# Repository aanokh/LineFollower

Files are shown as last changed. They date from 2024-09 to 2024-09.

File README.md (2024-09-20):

# __Line Follower Robot__

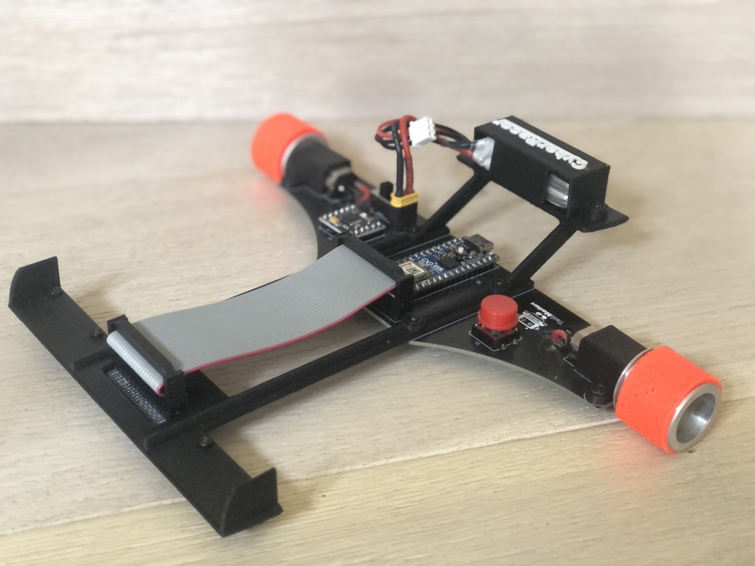
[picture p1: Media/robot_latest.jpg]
An image of the robot


This autonomous line follower robot was created for the RoboGames Olympics 2024 by me and my younger brother. It has been designed, modeled, constructed and programmed from scratch. The robot can autonomously follow a black or white line on a contrasting background at high speeds by implementing a PID controller.

### 3D Design

The bracket and other components of the robot body were designed in Autodesk Fusion 360. They were then sliced in Ultimaker Cuda and 3d printed, first out of plastic and finally from carbon fiber. The main frame was designed to be easily replaceable to test varying robot lengths and multiple prototypes were tried before arriving at the final design.

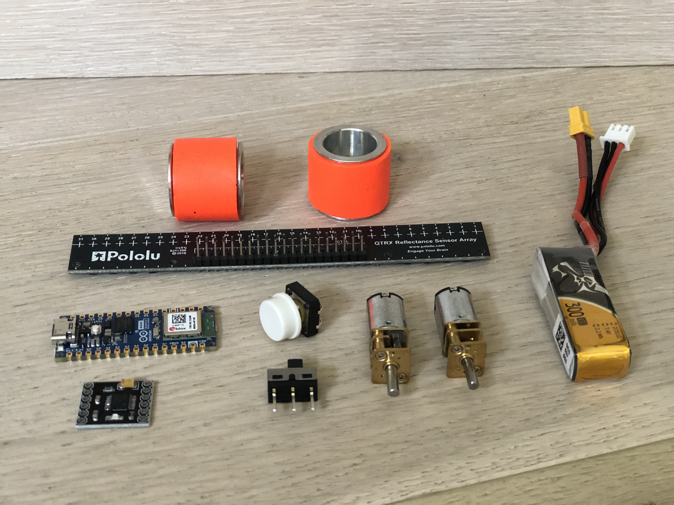
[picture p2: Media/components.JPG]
An image of some of the robot's components


After early testing, it was evident that standard rubber wheels were too slippery and hindered the robot's accuracy especially on sharp turns. To solve this issue, the wheels were upgraded to special JSumo non-slip aluminum silicone wheels that greatly increase the robot's friction with the track.

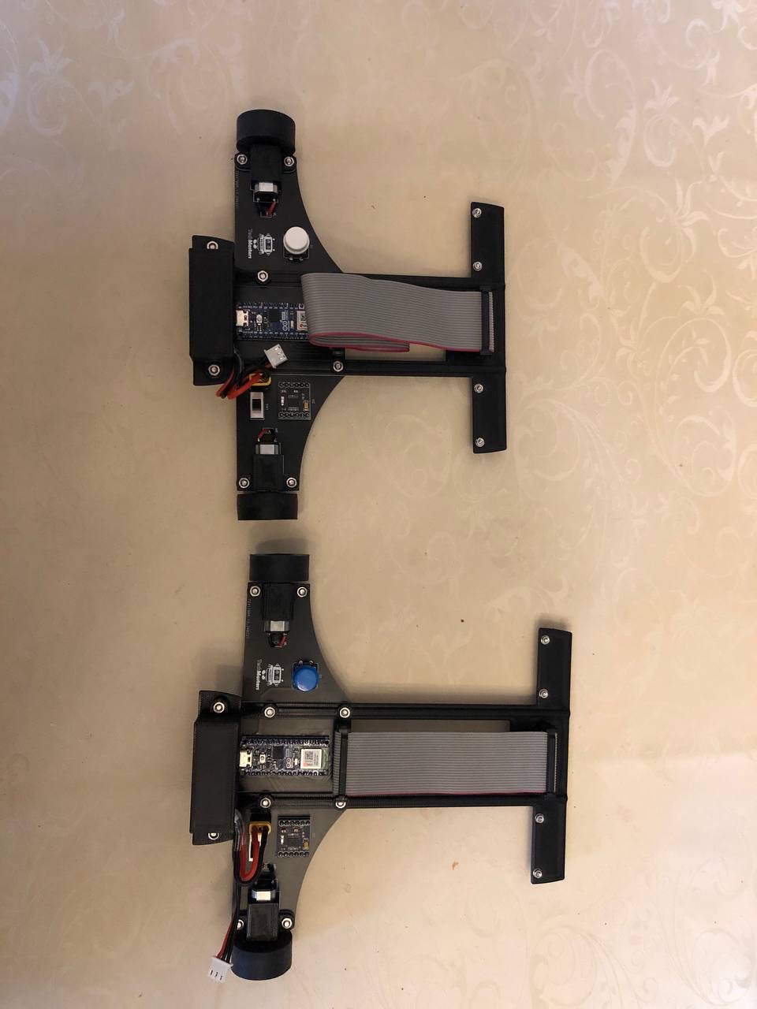
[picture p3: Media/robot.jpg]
An image of two older prototypes


### Electronics Design

An image of the PCB without components

The robot uses an Arduino Nano ESP32 Microcontroller, a DRV8833 Motor Drive Module, and a 16 channel Pololu QTR Reflectance Sensor Array. These components are mounted on a custom 2-sided PCB Board that was designed and manufactured with EasyEDA. The two 6V 1000RPM Pololu Micro Metal Gear Motors are powered by a rechargeable Lithium Polymer battery pack.

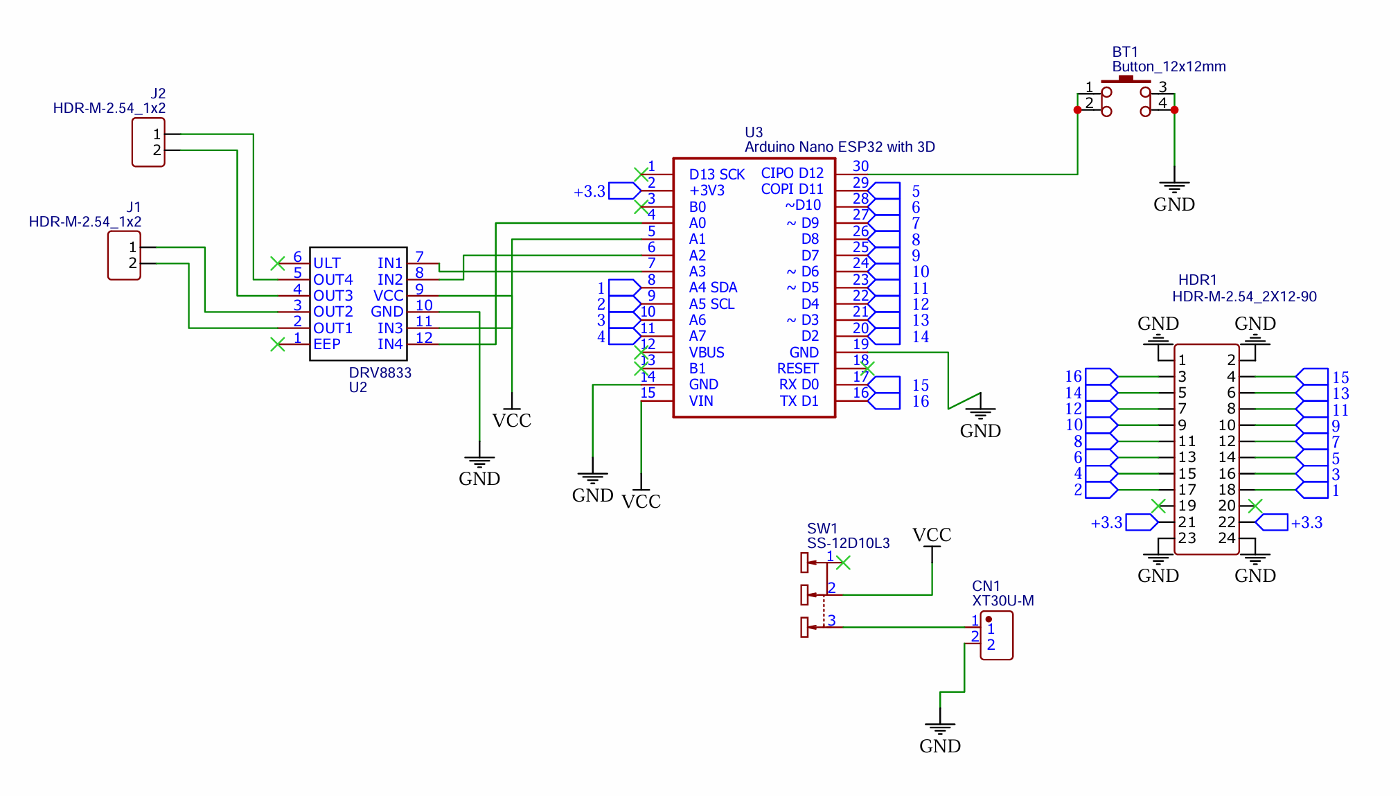
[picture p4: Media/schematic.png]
An image of the PCB schematic


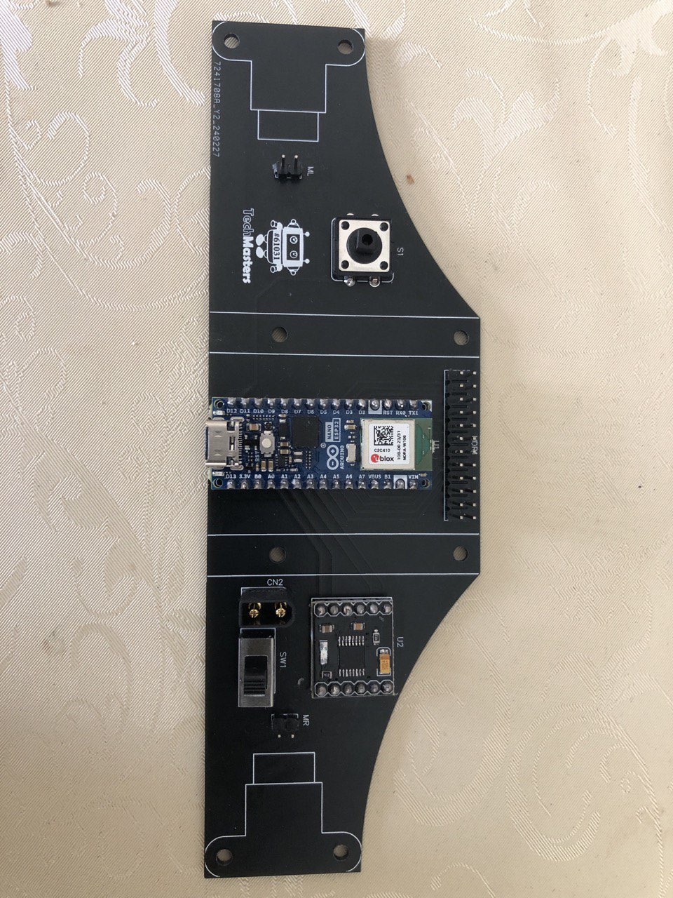
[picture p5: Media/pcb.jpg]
An image of the PCB


A stand-alone stopwatch device was also created for measuring the lap time of the robot.

### Software Design

Since the robot needs to keep the line sensor centered on the line while experiencing external changes, the PID controller algorithm was chosen for this task. In this scenario the target setpoint is the line position detected by the sensor, set to be held in the middle. The process affected by the outputs is the turning of the motors.

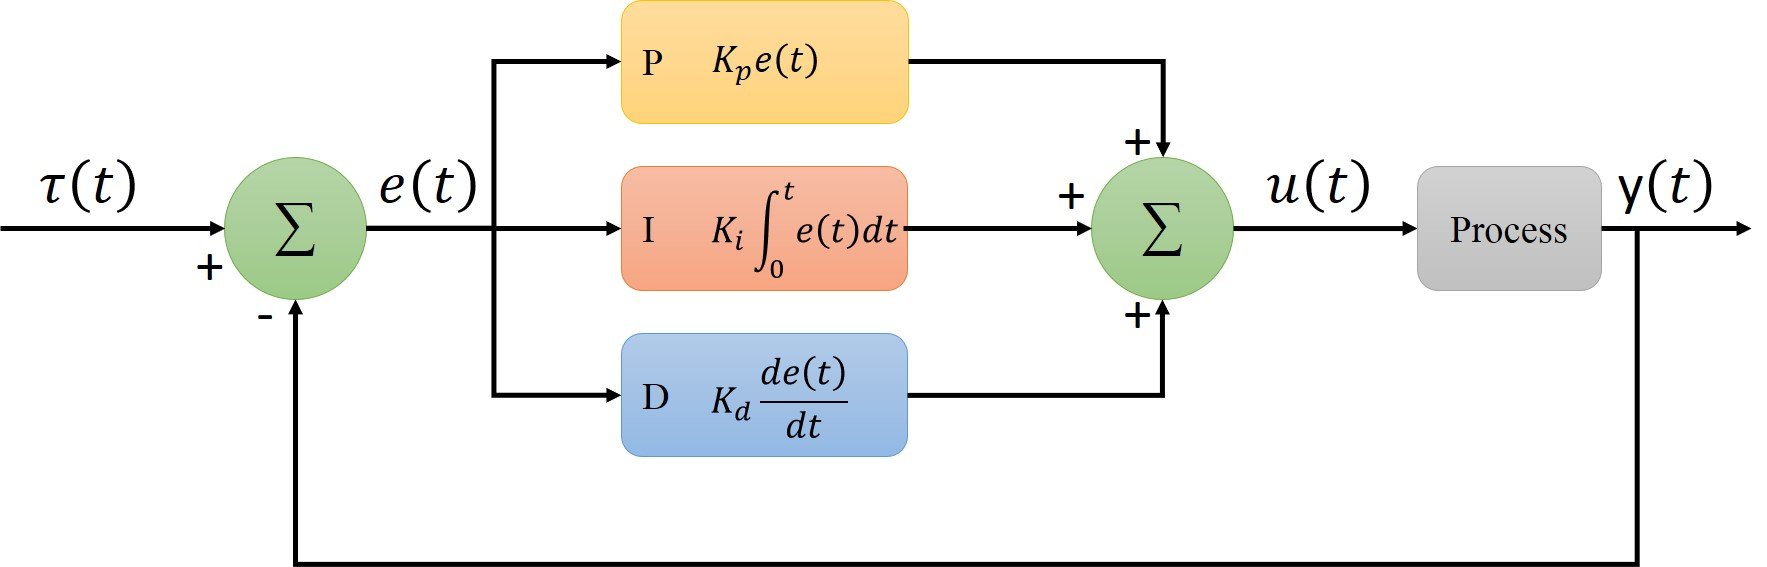
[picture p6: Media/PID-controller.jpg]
A diagram of the PID Controller


Each of the PID modules requires a coefficient, which is fine tuned by hand to optimally fit a given track. To expedite this process, a simple mobile application was created with MIT App Inventor which uses the Bluetooth Low Energy (BLE) technology to communicate with the Arduino microcontroller. This allows the coefficients to be quickly tweaked while observing the results in real time. When the desired coefficients are reached, they are serialized with the Arduino Preferences library.

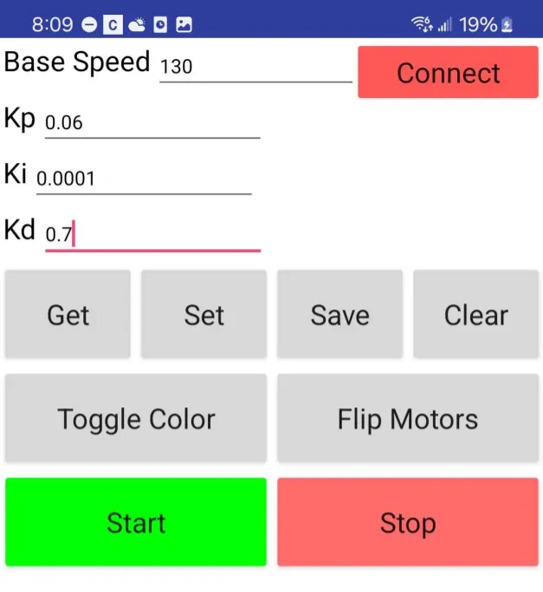
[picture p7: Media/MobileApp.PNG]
An image of the mobile app


### Result Videos

https://github.com/user-attachments/assets/4bbc2604-2ac1-476d-a4cd-80716923511e

### Future Improvements
A major improvement that could be made to the robot design is adding a turbine to improve the robot's friction.
The stopwatch device could be improved by letting it also connect to a mobile app and calculate the average lap time.
Multiple coefficient profiles could be added to support easy switching between tracks and frame lengths.

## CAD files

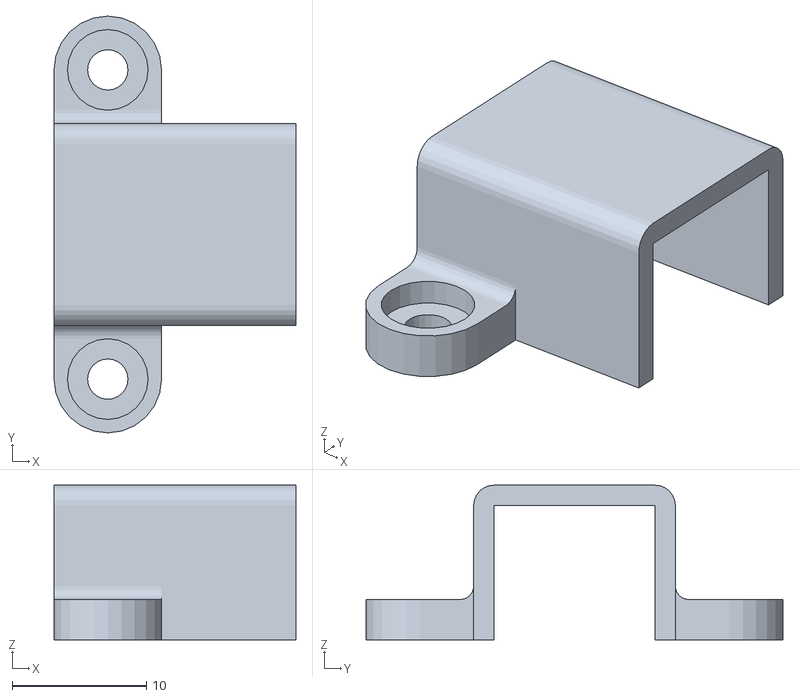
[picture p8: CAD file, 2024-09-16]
3D Design/motor_bracket.stl
18.0 x 31.0 x 11.5

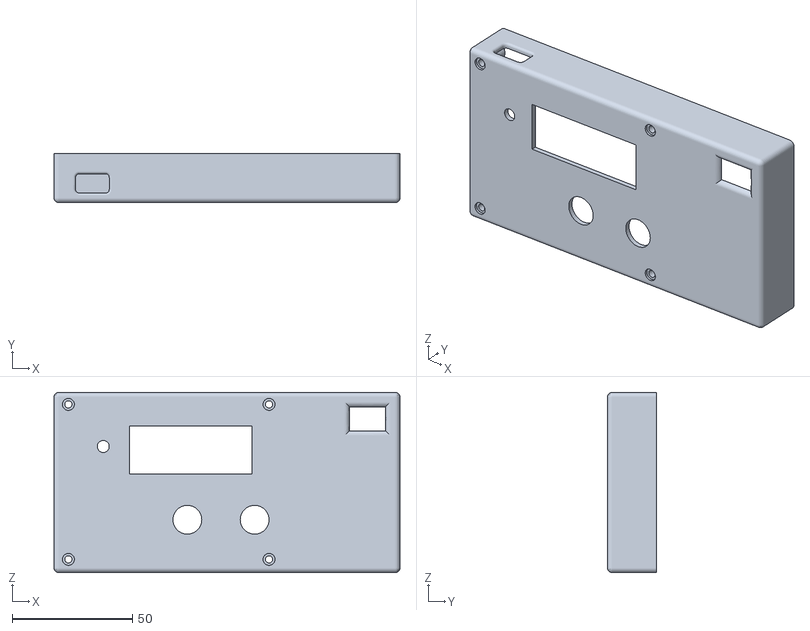
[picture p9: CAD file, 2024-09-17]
Stopwatch/stopwatch-box.stl
144.0 x 20.5 x 75.0

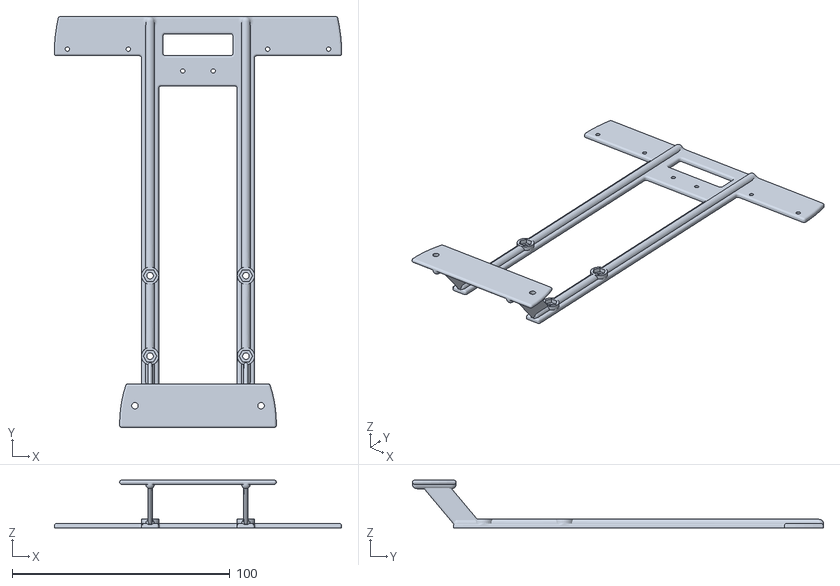
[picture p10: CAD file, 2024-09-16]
3D Design/frame_170.stl
132.0 x 188.8 x 22.0

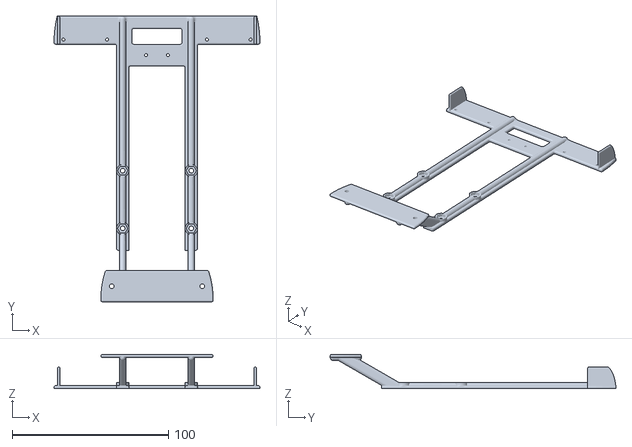
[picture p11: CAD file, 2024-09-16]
3D Design/frame_150.stl
132.0 x 183.0 x 22.0

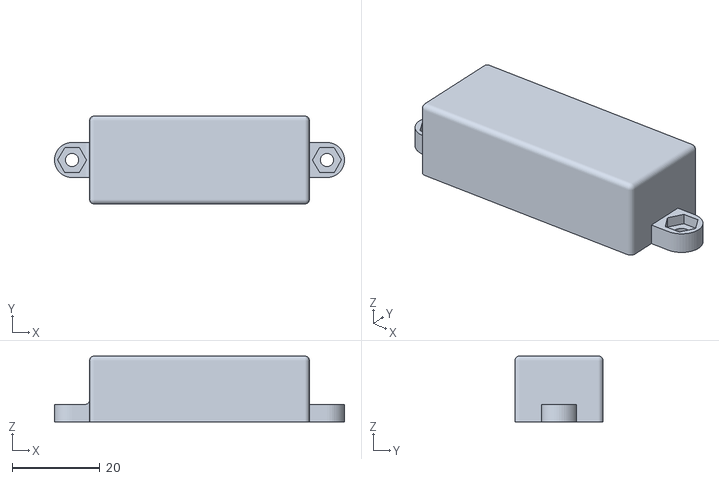
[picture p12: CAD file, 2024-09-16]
3D Design/battery_holder.stl
66.0 x 20.0 x 15.0

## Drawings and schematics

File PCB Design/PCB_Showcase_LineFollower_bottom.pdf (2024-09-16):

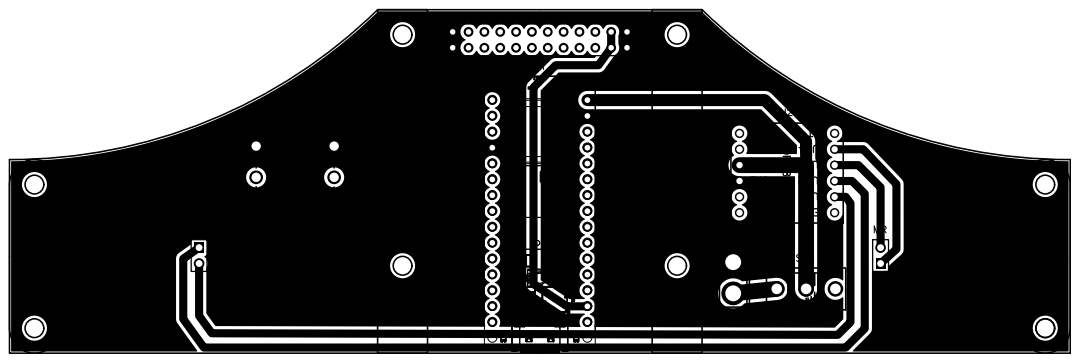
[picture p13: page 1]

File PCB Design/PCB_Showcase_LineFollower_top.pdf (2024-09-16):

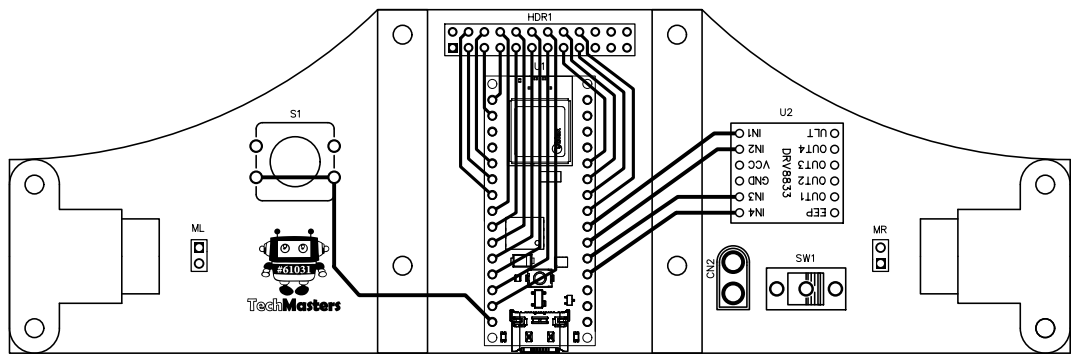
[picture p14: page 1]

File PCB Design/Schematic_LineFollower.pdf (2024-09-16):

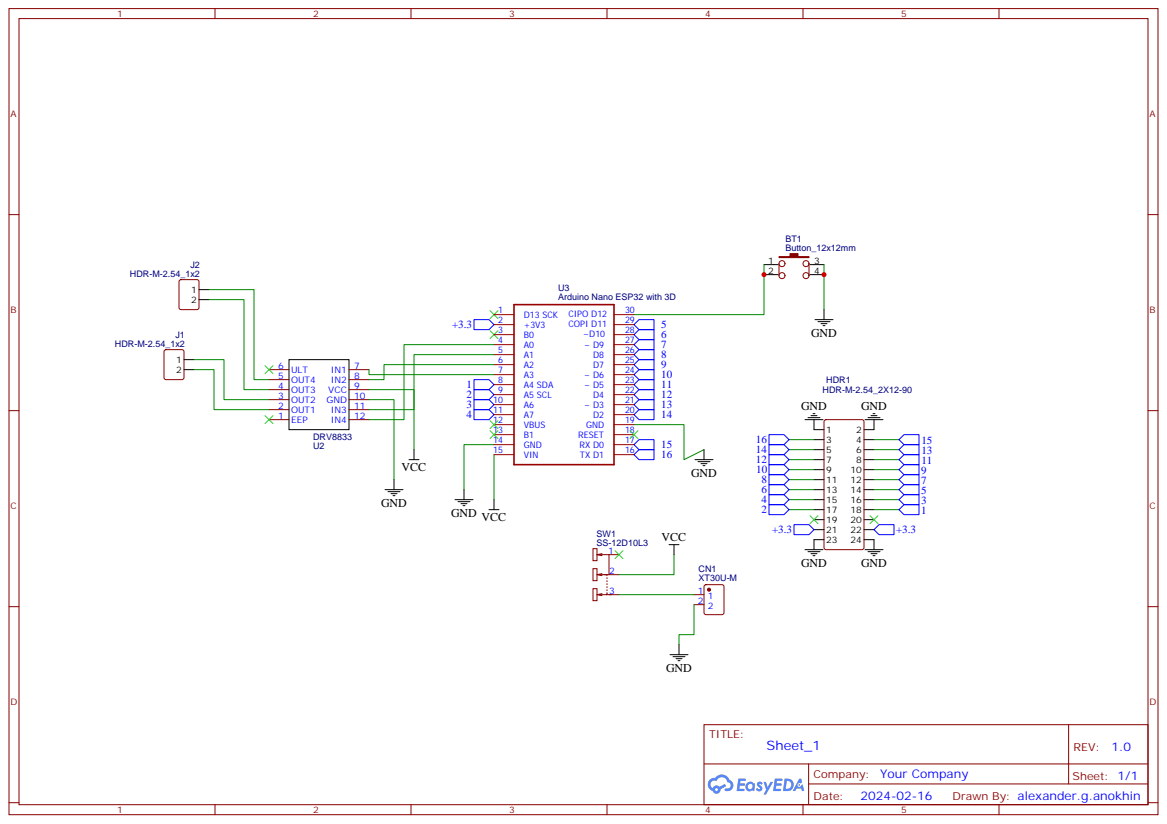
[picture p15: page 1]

Drawn By: alexander.g.anokhin

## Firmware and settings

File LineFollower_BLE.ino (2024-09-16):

#include "LineFollower.h"
#include "BLE_Control.h"
#include <QTRSensors.h>
#include <Preferences.h>
#include <AsyncTCP.h>
#include <Button.h>

#define IN1 20
#define IN2 19
#define IN3 17
#define IN4 18

#define RED 14
#define GREEN 15
#define BLUE 16

const int TARGET_VALUE = 7500;

float baseSpeed = 100;
int maxSpeed = 254;
bool running = false;

float kp = 0.02;
float ki = 0;
float kd = 0.45;

float p;
float i;
float d;
int correction;
float lastError;

bool readBlack = true;
bool flipMotors = false;

Button button(12);

const int PWM_FREQ = 500;     // Recall that Arduino Uno is ~490 Hz. Official ESP32 example uses 5,000Hz
const int PWM_RESOLUTION = 8;

Preferences prefs;

QTRSensors qtr;
const uint8_t sensorCount = 16;
uint16_t sensorValues[sensorCount];

bool calibrating = false;

void setup() {
  button.begin();
  pinMode(BLUE, OUTPUT);
  pinMode(RED, OUTPUT);
  pinMode(GREEN, OUTPUT);

  initLedc();

  // stop all motors
  drive(0, 0);

  Serial.begin(9600);
  //while(!Serial);
  Serial.println("Serial initialized");

  readCoefficients();

  setupBLE();

  qtr.setTypeRC();
  qtr.setSensorPins((const uint8_t[]){22, 21, 24, 23, 10, 11, 8, 9, 6, 7, 1, 5, 0, 2, 3, 4}, sensorCount);

  if (button.pressed()) {
    calibrating = true;
    while (!button.released());
  } else {
    light(RED);
  }

  if (calibrating) {
    while (!button.pressed());
    calibrateSensors();
  } else {
    readCalibration();
    // go to loop (wait for start from button or bluetooth)
  }

  /*
  while (!button.pressed());

  if (calibrating) {
    calibrateSensors();
  } else {
    readCalibration();
    start();
  }*/
}

void loop() {
  correction = PIDController(qtr.readLineBlack(sensorValues));

  if (running) {
    drive(constrain(baseSpeed + correction, -254, 254), constrain(baseSpeed - correction, -254, 254));
  } else {
    drive(0, 0);
  }

  if (button.pressed()) {
    if (running) {
      stop();
    } else {
      start();
    }
  }
}

void start() {
  if (calibrating) {
    return;
  }
  running = true;
  light(GREEN);
}

void stop() {
  if (calibrating) {
    return;
  }
  running = false;
  light(RED);
}

void calibrateSensors() {
  
  light(BLUE);

  for (uint16_t i = 0; i < 400; i++){
    qtr.calibrate();
  }

  // save to prefs
  if (qtr.calibrationOn.initialized) {
    prefs.begin("prefs", false);
    for (int i = 0; i < sensorCount; i++) {
      String maxKey = "max";
      String minKey = "min";
      maxKey += i;
      minKey += i;
      prefs.putUShort(maxKey.c_str(), qtr.calibrationOn.maximum[i]);
      prefs.putUShort(minKey.c_str(), qtr.calibrationOn.minimum[i]);
    }
    prefs.end();
  }

  light(RED);
  calibrating = false;
}

int PIDController(int value) {
  p = TARGET_VALUE - value;
  i += p;
  d = p - lastError;
  lastError = p;
  return kp * p + ki * i + kd * d;
}

void initLedc() {
  ledcSetup(1, PWM_FREQ, PWM_RESOLUTION);
  ledcSetup(2, PWM_FREQ, PWM_RESOLUTION);
  ledcSetup(3, PWM_FREQ, PWM_RESOLUTION);
  ledcSetup(4, PWM_FREQ, PWM_RESOLUTION);

  ledcAttachPin(IN1,1); 
  ledcAttachPin(IN2,2);
  ledcAttachPin(IN3,3);
  ledcAttachPin(IN4,4);
}

void readCoefficients() {
  prefs.begin("prefs", true); // true = read only
  if (prefs.isKey("bs")) {
    baseSpeed = prefs.getInt("bs");
  }
  if (prefs.isKey("ms")) {
    maxSpeed = prefs.getInt("ms");
  }
  if (prefs.isKey("kp")) {
    kp = prefs.getFloat("kp");
  }
  if (prefs.isKey("ki")) {
    ki = prefs.getFloat("ki");
  }
  if (prefs.isKey("kd")) {
    kd = prefs.getFloat("kd");
  }
  if (prefs.isKey("rb")) {
    readBlack = prefs.getBool("rb");
  }
  if (prefs.isKey("f")) {
    flipMotors = prefs.getBool("f");
  }
  prefs.end();
}

void readCalibration() {
  // dummy calibrate to create arrays
  qtr.calibrate();

  if (!qtr.calibrationOn.initialized) {
    return;
  }

  prefs.begin("prefs", true);
  for (int i = 0; i < sensorCount; i++) {
    String maxKey = "max";
    String minKey = "min";
    maxKey += i;
    minKey += i;
    if (prefs.isKey(maxKey.c_str())) {
      qtr.calibrationOn.maximum[i] = prefs.getUShort(maxKey.c_str());
    }
    if (prefs.isKey(minKey.c_str())) {
      qtr.calibrationOn.minimum[i] = prefs.getUShort(minKey.c_str());
    }
  }
  prefs.end();
}

void writeCoefficients() {
  prefs.begin("prefs", false); // false = read/write
  prefs.putInt("bs", baseSpeed);
  prefs.putInt("ms", maxSpeed);
  prefs.putFloat("kp", kp);
  prefs.putFloat("ki", ki);
  prefs.putFloat("kd", kd);
  prefs.putBool("rb", readBlack);
  prefs.putBool("f", flipMotors);
  prefs.end();
}

void drive(int leftMotor, int rightMotor) {
  if (flipMotors) {
    //driveInverted(leftMotor, rightMotor);
    //return;
  }

  if (leftMotor < 0) {
    // backward
    ledcWrite(1, abs(leftMotor));
    ledcWrite(2, 0);
  } else {
    // forward
    ledcWrite(1, 0);
    ledcWrite(2, leftMotor);
  }

  if (rightMotor < 0) {
    // backward
    ledcWrite(3, abs(rightMotor));
    ledcWrite(4, 0);
  } else {
    // forward
    ledcWrite(3, 0);
    ledcWrite(4, rightMotor);
  }
}

void driveInverted(int leftMotor, int rightMotor) {

  if (leftMotor < 0) {
    // backward
    ledcWrite(2, abs(leftMotor));
    ledcWrite(1, 0);
  } else {
    // forward
    ledcWrite(2, 0);
    ledcWrite(1, leftMotor);
  }

  if (rightMotor < 0) {
    // backward
    ledcWrite(4, abs(rightMotor));
    ledcWrite(3, 0);
  } else {
    // forward
    ledcWrite(4, 0);
    ledcWrite(3, rightMotor);
  }
}

void light(int pin) {
  // RED, GREEN, BLUE: LOW = ON!   HIGH = OFF!
  if (pin == RED) {
    digitalWrite(RED, LOW);
    digitalWrite(GREEN, HIGH);
    digitalWrite(BLUE, HIGH);
  } else if (pin == GREEN) {
    digitalWrite(GREEN, LOW);
    digitalWrite(RED, HIGH);
    digitalWrite(BLUE, HIGH);
  } else if (pin == BLUE) {
    digitalWrite(BLUE, LOW);
    digitalWrite(RED, HIGH);
    digitalWrite(GREEN, HIGH);
  } else if (pin == 0) {
    // all off
    digitalWrite(RED, HIGH);
    digitalWrite(GREEN, HIGH);
    digitalWrite(BLUE, HIGH);
  }
}

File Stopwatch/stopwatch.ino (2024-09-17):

#include <TM1637Display.h>
#include <Button.h>

#define CLOCK 18
#define IO 19
#define SENSOR 5

Button buttonA(22);
Button buttonB(21);

TM1637Display display(CLOCK, IO);
int secs = 0;
long lastMillis;
long fastestTime = 0;
uint8_t data[4];


void setup() {
  pinMode(17, INPUT);
  buttonA.begin();
  buttonB.begin();
  display.setBrightness(0x0f);
  data[0] = display.encodeDigit(0);
  data[1] = display.encodeDigit(0);
  data[2] = display.encodeDigit(0);
  data[3] = display.encodeDigit(0);
  display.setSegments(data);
  while (!buttonA.pressed());
}

void loop() {
  //display.setSegments(data);
  //display.showNumberDecEx(millis()/10,0b01000000,true);
  if (!digitalRead(SENSOR)) {
    reset();
  }
}

void reset() {
  display.showNumberDecEx((millis() - lastMillis)/10,0b01000000,false);
  if (fastestTime == 0 || (millis() - lastMillis) < fastestTime) {
    fastestTime = millis() - lastMillis;
  }
  lastMillis = millis();
  delay(300);
}

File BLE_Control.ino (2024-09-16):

#include "LineFollower.h"
#include <BLEDevice.h>
#include <BLEUtils.h>
#include <BLEServer.h>
#include <BLE2902.h>

// See the following for generating UUIDs:
// https://www.uuidgenerator.net/

#define DEVICE_NAME "TM"
#define SERVICE_UUID "3f8a4ae3-cc48-4955-afda-4f2a01d49ec7"
#define KP_UUID "562b2a0b-5752-4f00-8af9-01f7ac0e4bed"
#define KI_UUID "1762ba84-e7c2-4fc8-a70d-8450e6ec010e"
#define KD_UUID "8745bcc3-01a8-4480-ba40-09cbf72bc2f3"
#define CMD_UUID "04eba61a-2f33-45f8-bfce-2843384c56cf"
#define BASESPEED_UUID "39e569ae-a1b0-4f9c-9346-7825cc8eaafd"
#define MAXSPEED_UUID "5f3f3c58-dc9b-4e3a-aa27-4f762e5a14da"

BLEServer* pServer = NULL;

BLECharacteristic* pKp = NULL;
BLECharacteristic* pKi = NULL;
BLECharacteristic* pKd = NULL;
BLECharacteristic* pCmd = NULL;
BLECharacteristic* pBaseSpeed = NULL;

class MyServerCallbacks: public BLEServerCallbacks {
    void onConnect(BLEServer* pServer) {
      digitalWrite(LED_BUILTIN,HIGH);
      Serial.println("Client Connected");
    };

    void onDisconnect(BLEServer* pServer) {
      digitalWrite(LED_BUILTIN,LOW);
      Serial.println("Client Disconnected");
      BLEDevice::startAdvertising();
    }
};

class MyCallbacks: public BLECharacteristicCallbacks {
    void onWrite(BLECharacteristic *pCharacteristic) {
      String uuid = String(pCharacteristic->getUUID().toString().c_str());
      if (uuid == KP_UUID){
        kp = atof(pCharacteristic->getValue().c_str());
      } else if (uuid == KI_UUID){
        ki = atof(pCharacteristic->getValue().c_str());
      } else if (uuid == KD_UUID){
        kd = atof(pCharacteristic->getValue().c_str());
      } else if (uuid == CMD_UUID){
        int cmd = atoi(pCharacteristic->getValue().c_str());
        switch (cmd) {
          case 0:
            stop();
            Serial.println("Stop");
            break;
          case 1:
            start();
            Serial.println("Start");
            break;
          case 2:
            // write properties
            Serial.println("Save");
            break;
          default:
            Serial.println("Wrong command");
        }
      } else if (uuid == BASESPEED_UUID){
        baseSpeed = atof(pCharacteristic->getValue().c_str());
      }
      Serial.print("Received value ");
      Serial.println(pCharacteristic->getValue().c_str());
    }

    void onRead(BLECharacteristic *pCharacteristic) {
      String uuid = String(pCharacteristic->getUUID().toString().c_str());
      if (uuid == KP_UUID){
        pCharacteristic->setValue(kp);
      } else if (uuid == KI_UUID){
        pCharacteristic->setValue(ki);
      } else if (uuid == KD_UUID){
        pCharacteristic->setValue(kd);
      } else if (uuid == BASESPEED_UUID){
        pCharacteristic->setValue(baseSpeed);
      }
      Serial.println("Sent value");
    }

};

void setupBLE() {
  pinMode(LED_BUILTIN, OUTPUT);
  digitalWrite(LED_BUILTIN, LOW);

  // Create the BLE Device
  BLEDevice::init(DEVICE_NAME);

  // Create the BLE Server
  pServer = BLEDevice::createServer();
  pServer->setCallbacks(new MyServerCallbacks());

  // Create the BLE Service
  BLEService *pService = pServer->createService(SERVICE_UUID);

  BLECharacteristic *pKp = pService->createCharacteristic(
                                         KP_UUID,
                                         BLECharacteristic::PROPERTY_READ |
                                         BLECharacteristic::PROPERTY_WRITE
                                       );
  BLECharacteristic *pKi = pService->createCharacteristic(
                                         KI_UUID,
                                         BLECharacteristic::PROPERTY_READ |
                                         BLECharacteristic::PROPERTY_WRITE
                                       );
  BLECharacteristic *pKd = pService->createCharacteristic(
                                         KD_UUID,
                                         BLECharacteristic::PROPERTY_READ |
                                         BLECharacteristic::PROPERTY_WRITE
                                       );
  BLECharacteristic *pCmd = pService->createCharacteristic(
                                         CMD_UUID,
                                         BLECharacteristic::PROPERTY_WRITE
                                       );
  BLECharacteristic *pBaseSpeed = pService->createCharacteristic(
                                         BASESPEED_UUID,
                                         BLECharacteristic::PROPERTY_READ |
                                         BLECharacteristic::PROPERTY_WRITE
                                       );

  pKp->setCallbacks(new MyCallbacks());
  pKp->setValue(kp);

  pKi->setCallbacks(new MyCallbacks());
  pKi->setValue(ki);

  pKd->setCallbacks(new MyCallbacks());
  pKd->setValue(kd);

  pBaseSpeed->setCallbacks(new MyCallbacks());
  pBaseSpeed->setValue(baseSpeed);

  pCmd->setCallbacks(new MyCallbacks());
  
  // https://www.bluetooth.com/specifications/gatt/viewer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
  // Create a BLE Descriptor
  pKp->addDescriptor(new BLE2902());
  pKi->addDescriptor(new BLE2902());
  pKd->addDescriptor(new BLE2902());
  pBaseSpeed->addDescriptor(new BLE2902());
  pCmd->addDescriptor(new BLE2902());
  
  // Start the service
  pService->start();

  //BLEAdvertising *pAdvertising = pServer->getAdvertising();
  //pAdvertising->start();
  
  // Start advertising
  BLEAdvertising *pAdvertising = BLEDevice::getAdvertising();
  pAdvertising->addServiceUUID(SERVICE_UUID);
  pAdvertising->setScanResponse(false);
  pAdvertising->setMinPreferred(0x0);  // set value to 0x00 to not advertise this parameter
  BLEDevice::startAdvertising();
  Serial.println("Waiting a client connection to notify...");
}

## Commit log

2024-09-16 File upload
    [Bracket_Motor.stl, battery_holder.stl, frame_150_final.stl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]
2024-09-17 stopwatch box
    [stopwatch-box.stl]
2024-09-19 schematic picture
2024-09-20 mobile app image
    [frame_150.stl, frame_170.stl, motor_bracket.stl]
